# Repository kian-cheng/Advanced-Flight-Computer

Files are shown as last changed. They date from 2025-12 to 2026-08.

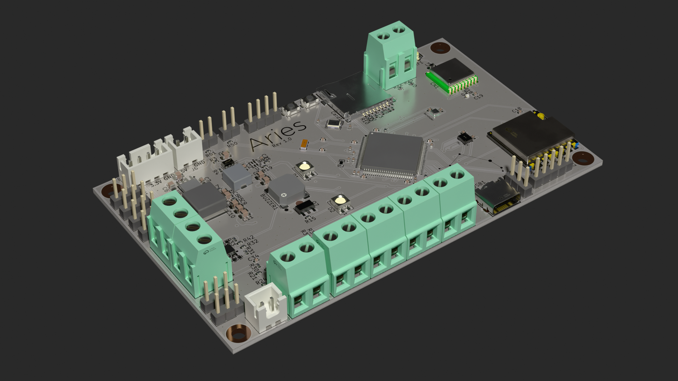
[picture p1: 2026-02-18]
CAD/Aries render.png

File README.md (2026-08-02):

# Advanced-Flight-Computer
A flight computer designed to be feature-rich and intuitive to use. Include features for dual deployment, ignition, active flight stabilisation and data logging. 

Before this, I've only made a simpler flight computer on a perfboard that does data logging and managing ignition and ejection. So this is my oppoturnity to make something more advanced on a PCB. 



## Features

- MCU: STM32H743VIT6
- Barometer: BMP 580
- IMU: ICM-45686
- GPS: ATGM336
- LORA: Ra-02
- USB-C
- Micro SD card reader
- 6 pyro channels
- 6 servo channels

## Schematic



## PCB layout





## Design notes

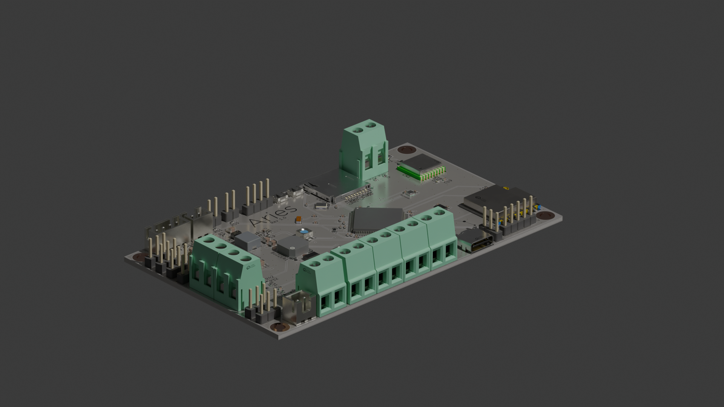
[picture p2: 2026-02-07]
CAD/Aries first render.png

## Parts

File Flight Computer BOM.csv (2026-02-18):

Item | Description | Cost (USD) | Quantity | Link
PCB + PCBA | 4 layer PCB from JLCPCB including shipping, although the ICM-45686 is out of stock so a 26 USD + shipping budget should be considered for getting it in the future. (2 is the minimum) | 289.85 | 1
PCB Shipping | Cheapest available SF express | 11.36 | 1
RF Antenna | For RA-02 433Mhz | 3.99 | 1 | https://www.waveshare.com/sma-433-antenna.htm
GPS Antenna | For GPS | 1.99 | 1 | https://www.waveshare.com/gnss-ceramic-antenna.htm
IPX to SMA | IPEX 1 specifically for RA-02 to Antenna | 0.69 | 1 | https://www.waveshare.com/sma-to-ipex-cable.htm?sku=21119
Waveshare shipping | Shipping for the three products above, cheapest available | 6 | 1
ICM-45686 | LCSC (only applicable when out of stock and backorder is needed) | 13.69 | 2 | https://www.lcsc.com/product-detail/C22459454.html
1x05 pins | LCSC (MPQ20) | 0.48 | 1 | https://www.lcsc.com/product-detail/C42431835.html?s_z=n_1x05
1x04 pins | LCSC (MPQ20) | 0.35 | 1 | https://www.lcsc.com/product-detail/C52016392.html
1x02 pins | LCSC (MPQ20) | 0.28 | 1 | https://www.lcsc.com/product-detail/C52016390.html
JST XH 4 pin | LCSC (MPQ10) | 0.53 | 1 | https://www.lcsc.com/product-detail/C144395.html?s_z=n_jst%2520xh%25204%2520pin
JST XH 2 pin | LCSC (MPQ20) | 0.71 | 1 | https://www.lcsc.com/product-detail/C158012.html
LCSC Shipping | Cheapest available | 5.51 | 1
Solder paste | Shipping can be free with vouchers (only required when ICM-45686 is out of stock) | 8.87 | 1 | https://shopee.com.my/product/279893497/15397824526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

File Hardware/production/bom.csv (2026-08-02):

Designator | Footprint | Quantity | Value | LCSC Part #
BUZZER1 | BUZ-SMD_4P-L7.5-W7.5-P7.59-TL | 1 | MLT-7525 | C95299
C1 | 0805 | 1 | 2.2 uf
C10, C11, C3, C4, C9 | 0805 | 5 | 22uF
C12 | 0603 | 1 | 2.7nF
C13 | 0603 | 1 | 33pF
C14, C15, C16, C17, C20, C21, C22, C23, C24, C25, C26, C31, C32 | 0402 | 13 | 100nF
C18 | 0402 | 1 | 0.1uF
C19 | 0402 | 1 | 10uF
C2, C7 | 0603 | 2 | 100nF
C27 | 0402 | 1 | 10pF
C28, C29 | 0402 | 2 | 2.2uF
C30, C33 | 0402 | 2 | 1uF
C34 | 0402 | 1 | 22nF
C36 | 0402 | 1 | 4.7uF
C37, C38, C39, C40 | 0402 | 4 | 20pF
C5 | 0805 | 1 | 10uF
C6 | 0805 | 1 | 10nF
C8 | 0805 | 1 | 47pF
CARD1 | TF-SMD_TF-01A | 1 | TF-01A | C91145
CN1 | COMM-SMD_18P-L10.1-W9.7-P1.1-TL_L76-LB | 1 | ATGM336H-6N-74 | C5804601
D1, D2 | LED_SK6812MINI_PLCC4_3.5x3.5mm_P1.75mm | 2 | SK6812MINI
D10, D3, D6, D7, D8, D9 | 0402 | 6 | LED | C25503345
D11 | 0402 | 1 | LED | C130723
D4 | 0402 | 1 | LED | C21260817
D5 | 0603 | 1 | LED | C22371297
J1 | PinHeader_1x03_P2.54mm_Vertical | 1 | Conn_01x03_Pin
J2 | PinHeader_1x04_P2.54mm_Vertical | 1 | Conn_01x04_Pin
J3, J4 | PinHeader_1x02_P2.54mm_Vertical | 2 | Conn_01x02_Pin
J5, J6 | JST_XH_B2B-XH-AM_1x02_P2.50mm_Vertical | 2 | Conn_01x02_Pin | C158012
J7 | PinHeader_1x05_P2.54mm_Vertical | 1 | Conn_01x05_Pin
J8 | JST_XH_B4B-XH-AM_1x04_P2.50mm_Vertical | 1 | Conn_01x04_Pin
L1 | L_Bourns_SRP5030T | 1 | 5.6uH | C46595886
L2 | L_Cenker_CKCS8040 | 1 | 3.6uH | C223037
L3 | 0603 | 1 | 47nH | C98076
L4 | L0603 | 1 | FCM1608KF-601T03 | C141723
M1, M2, M3, M4, M5, M6 | PinHeader_1x03_P2.54mm_Vertical | 6 | Motor_Servo
P1, P2, P3, P4, P5, P6, P7, P8 | CONN-TH_2P-P5.00_WJ500V-5.08-2P | 8 | WJ500V-5.08-2P-14-00A | C8465
Q1, Q2, Q3 | POWER-1212-8_L3.3-W3.3-P0.66-LS3.3-BL | 3 | SI7232DN-T1-GE3 | C144854
Q7 | SOT-89-3_L4.5-W2.4-P1.50-LS4.0-BR | 1 | 2N2222AU | C21714170
R1, R2 | 0402 | 2 | 5.1K
R10, R11, R12, R13, R14, R19, R30, R31, R33, R37, R38, R40, R41, R50, R51, R8, R9 | 0402 | 17 | 10K
R15, R16, R18, R25, R26, R27, R28, R32, R34, R35, R36, R39, R42, R43 | 0402 | 14 | 1k
R17 | 0402 | 1 | 470
R20, R4, R6 | 0402 | 3 | 22.1k
R21 | 0402 | 1 | 120k
R22 | 0402 | 1 | 200K
R23 | 0402 | 1 | 40K
R24 | 0402 | 1 | 550
R29 | 0402 | 1 | 75k
R3 | 0402 | 1 | 100k
R44 | 0402 | 1 | 430
R5 | 0402 | 1 | 115k
R7 | 0402 | 1 | 15.8k
RF1 | IPEX-SMD_BWIPX-1-001E | 1 | BWIPX-1-001E | C496552
SW1, SW2 | SW-SMD_L3.9-W3.0-P4.45 | 2 | TS-1088-AR02016 | C720477
U1 | LGA-10_L2.0-W2.0-P0.50-TL_BMP580 | 1 | BMP580 | C22391138
U10, U11, U12, U13, U8, U9 | F0603 | 6 | 0438006.WRGT | C206962
U2 | LQFP-100_14x14mm_P0.5mm | 1 | STM32H743VITx | C114409
U3 | LGA-14_L3.0-W2.5-P0.50-TL | 1 | ICM-45686 | C22459454
U4 | SOT-23-6_L2.9-W1.6-P0.95-LS2.8-BL | 1 | LMR51430XDDCR | C5185863
U5 | SOIC-8_L4.9-W3.9-P1.27-LS6.0-BL-EP-1 | 1 | AP64501SP-13 | C2071517
U6 | WIRELM-SMD_RA-02-BL | 1 | RA-02 | C90039
U7 | VQFN-HR-12_L2.5-W2.0-P0.50-BL | 1 | TPS2121RUXR | C485916
USB1 | USB-C-SMD_TYPE-C16PIN | 1 | TYPE-C16PIN | C393939
X1 | CRYSTAL-SMD_4P-L3.2-W2.5-BL | 1 | X322525MOB4SI | C9006
X2 | FC-135R_L3.2-W1.5 | 1 | Q13FC1350000400 | C32346

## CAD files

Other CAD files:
CAD/Aries.blend

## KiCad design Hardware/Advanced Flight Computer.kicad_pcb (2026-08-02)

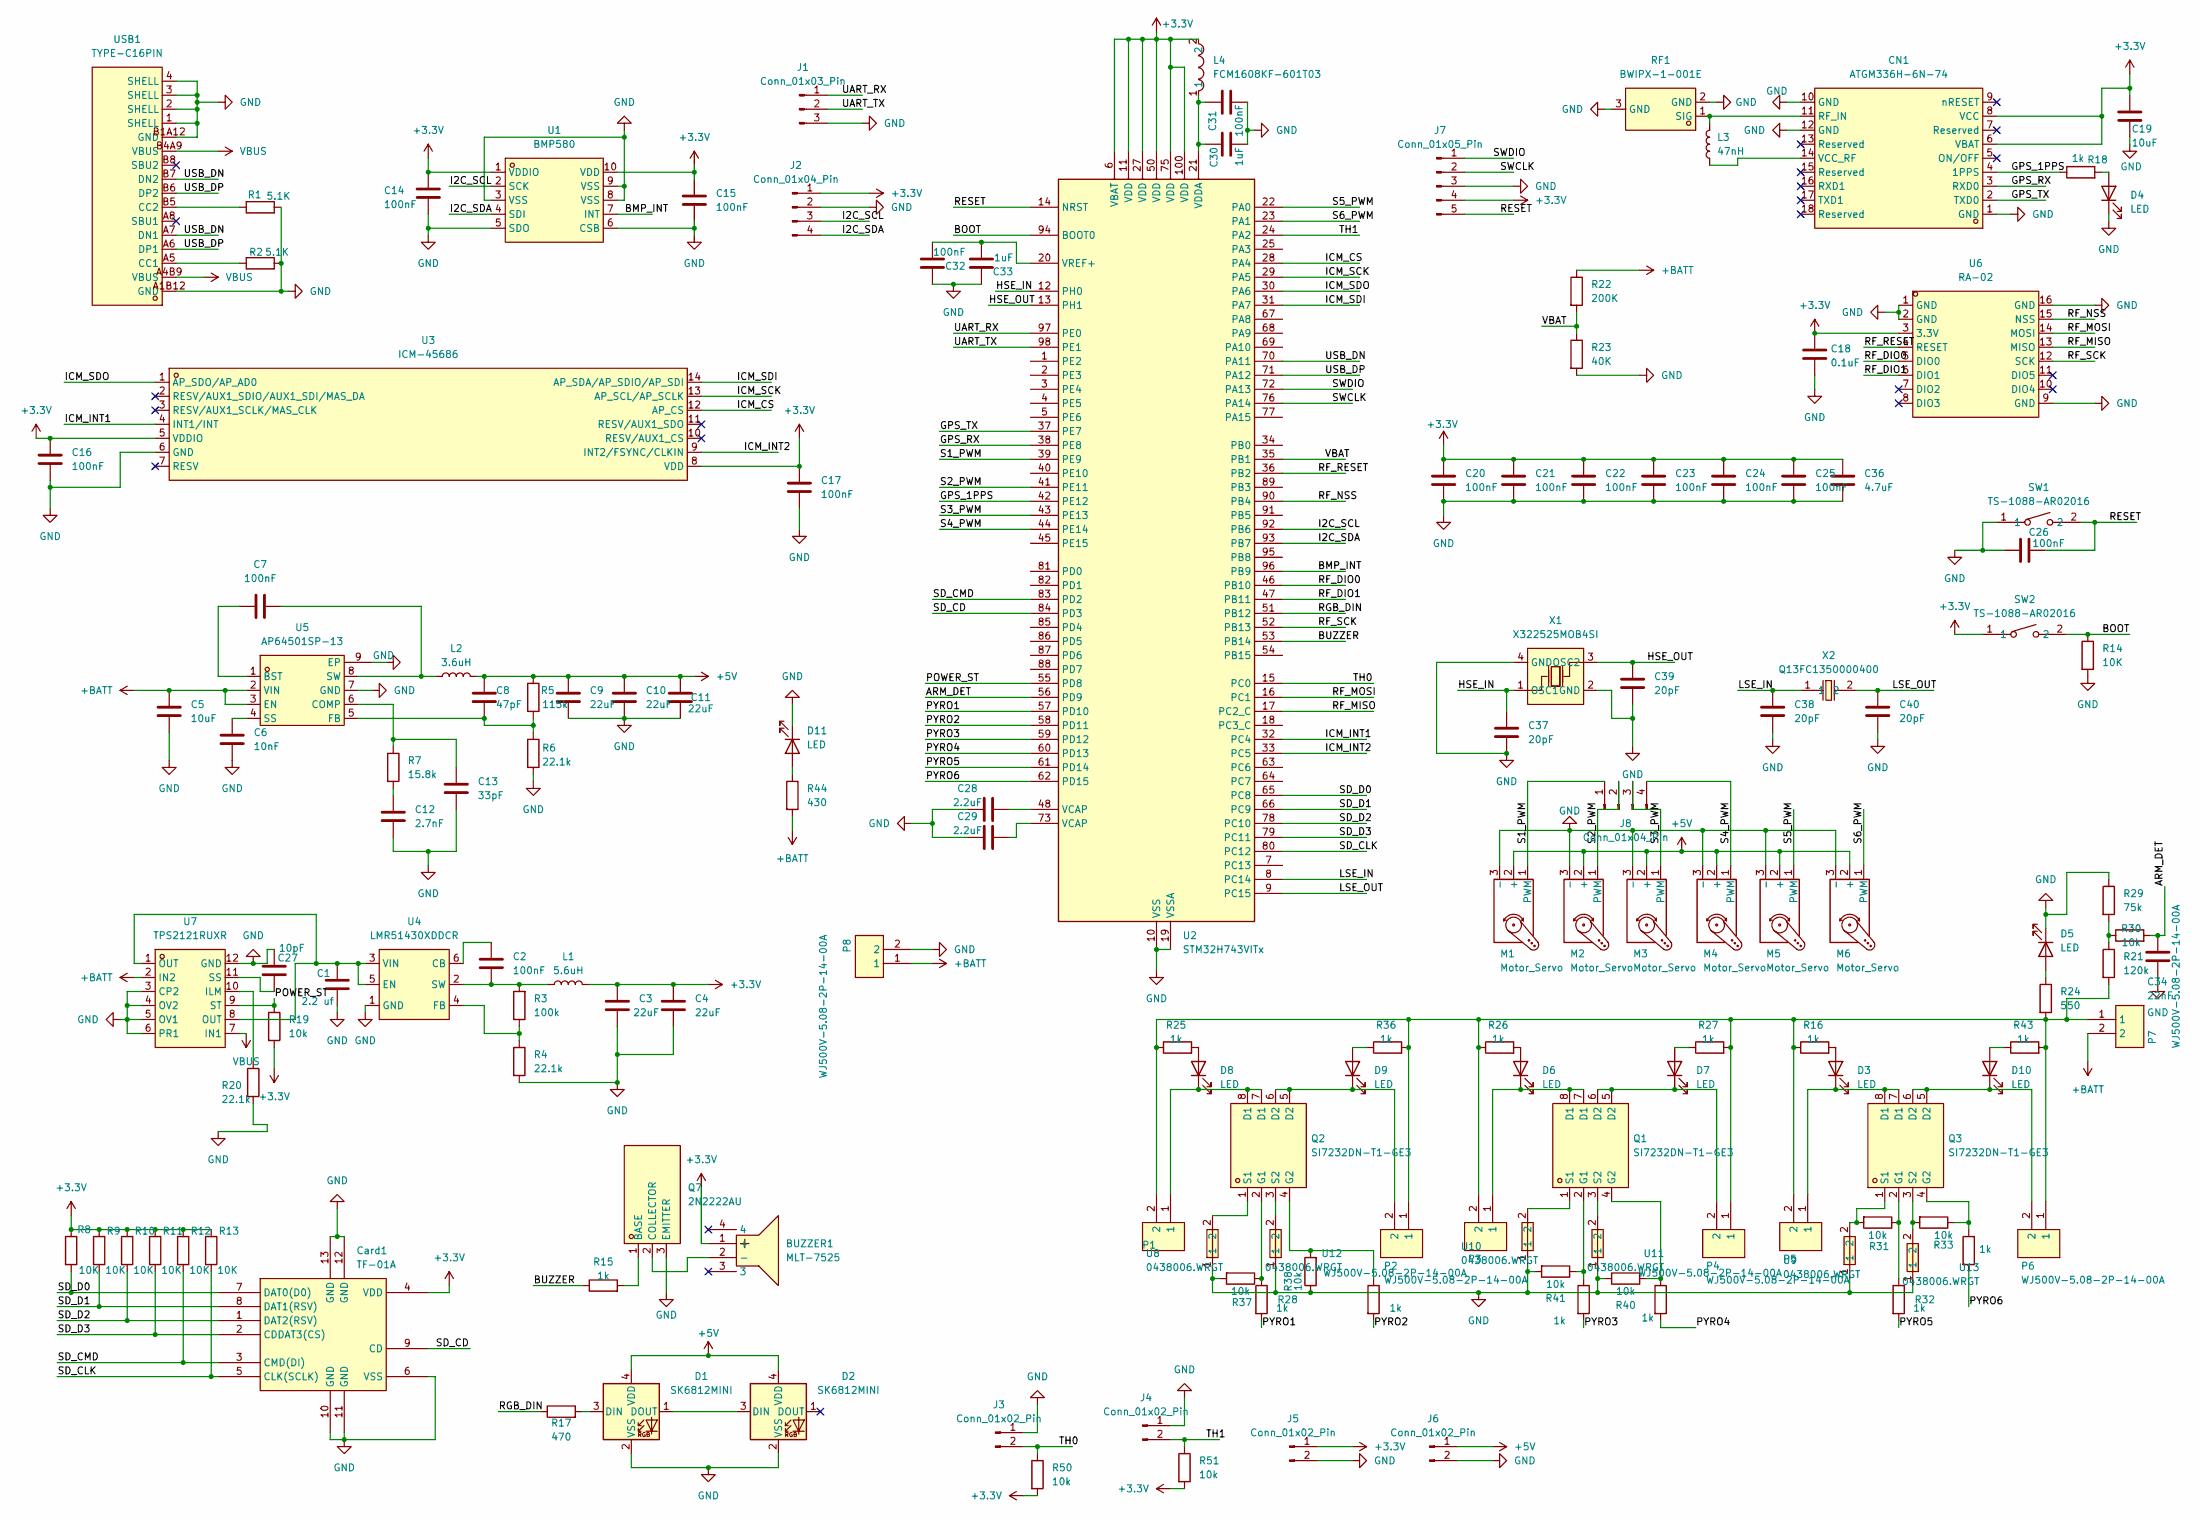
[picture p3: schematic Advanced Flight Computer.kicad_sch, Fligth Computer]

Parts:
BUZZER1: MLT-7525; BUZ-SMD_4P-L7.5-W7.5-P7.59-TL; LCSC Part C95299
C1: 2.2 uf; C_0805_2012Metric
C2, C7: 100nF; C_0603_1608Metric
C3, C4, C9, C10, C11: 22uF; C_0805_2012Metric
C5: 10uF; C_0805_2012Metric
C6: 10nF; C_0805_2012Metric
C8: 47pF; C_0805_2012Metric
C12: 2.7nF; C_0603_1608Metric
C13: 33pF; C_0603_1608Metric
C14, C15, C16, C17, C20, C21, C22, C23, C24, C25, C26, C31, C32: 100nF; C_0402_1005Metric
C18: 0.1uF; C_0402_1005Metric
C19: 10uF; C_0402_1005Metric
C27: 10pF; C_0402_1005Metric
C28, C29: 2.2uF; C_0402_1005Metric
C30, C33: 1uF; C_0402_1005Metric
C34: 22nF; C_0402_1005Metric
C36: 4.7uF; C_0402_1005Metric
C37, C38, C39, C40: 20pF; C_0402_1005Metric
CN1: ATGM336H-6N-74; COMM-SMD_18P-L10.1-W9.7-P1.1-TL_L76-LB; LCSC Part C5804601
Card1: TF-01A; TF-SMD_TF-01A; LCSC Part C91145
D1, D2: SK6812MINI; LED_SK6812MINI_PLCC4_3.5x3.5mm_P1.75mm
D3, D4, D6, D7, D8, D9, D10: LED; LED_0402_1005Metric
D5: LED; LED_0603_1608Metric
D11: LED; LED_0402_1005Metric; LCSC C130723
J1: Conn_01x03_Pin; PinHeader_1x03_P2.54mm_Vertical
J2: Conn_01x04_Pin; PinHeader_1x04_P2.54mm_Vertical
J3, J4: Conn_01x02_Pin; PinHeader_1x02_P2.54mm_Vertical
J5, J6: Conn_01x02_Pin; JST_XH_B2B-XH-AM_1x02_P2.50mm_Vertical; LCSC C158012
J7: Conn_01x05_Pin; PinHeader_1x05_P2.54mm_Vertical
J8: Conn_01x04_Pin; JST_XH_B4B-XH-AM_1x04_P2.50mm_Vertical
L1: 5.6uH; L_Bourns_SRP5030T; LCSC C46595886
L2: 3.6uH; L_Cenker_CKCS8040; LCSC C223037
L3: 47nH; L_0603_1608Metric_Pad1.05x0.95mm_HandSolder; LCSC C98076
L4: FCM1608KF-601T03; L0603; LCSC Part C141723
M1, M2, M3, M4, M5, M6: Motor_Servo; PinHeader_1x03_P2.54mm_Vertical
P1, P2, P3, P4, P5, P6, P7, P8: WJ500V-5.08-2P-14-00A; CONN-TH_2P-P5.00_WJ500V-5.08-2P; LCSC Part C8465
Q1, Q2, Q3: SI7232DN-T1-GE3; POWER-1212-8_L3.3-W3.3-P0.66-LS3.3-BL; LCSC Part C144854
Q7: 2N2222AU; SOT-89-3_L4.5-W2.4-P1.50-LS4.0-BR; LCSC Part C21714170
R1, R2: 5.1K; R_0402_1005Metric
R3: 100k; R_0402_1005Metric
R4, R6, R20: 22.1k; R_0402_1005Metric
R5: 115k; R_0402_1005Metric
R7: 15.8k; R_0402_1005Metric
R8, R9, R10, R11, R12, R13, R14: 10K; R_0402_1005Metric
R15, R16, R18, R25, R26, R27, R28, R32, R34, R35, R36, R39, R42, R43: 1k; R_0402_1005Metric
R17: 470; R_0402_1005Metric
R19, R30, R31, R33, R37, R38, R40, R41, R50, R51: 10k; R_0402_1005Metric
R21: 120k; R_0402_1005Metric
R22: 200K; R_0402_1005Metric
R23: 40K; R_0402_1005Metric
R24: 550; R_0402_1005Metric
R29: 75k; R_0402_1005Metric
R44: 430; R_0402_1005Metric
RF1: BWIPX-1-001E; IPEX-SMD_BWIPX-1-001E; LCSC Part C496552
SW1, SW2: TS-1088-AR02016; SW-SMD_L3.9-W3.0-P4.45; LCSC Part C720477
U1: BMP580; LGA-10_L2.0-W2.0-P0.50-TL_BMP580; LCSC Part C22391138
U2: STM32H743VITx; LQFP-100_14x14mm_P0.5mm
U3: ICM-45686; LGA-14_L3.0-W2.5-P0.50-TL; LCSC Part C22459454
U4: LMR51430XDDCR; SOT-23-6_L2.9-W1.6-P0.95-LS2.8-BL; LCSC Part C5185863
U5: AP64501SP-13; SOIC-8_L4.9-W3.9-P1.27-LS6.0-BL-EP-1; LCSC Part C2071517
U6: RA-02; WIRELM-SMD_RA-02-BL; LCSC Part C90039
U7: TPS2121RUXR; VQFN-HR-12_L2.5-W2.0-P0.50-BL; LCSC Part C485916
U8, U9, U10, U11, U12, U13: 0438006.WRGT; F0603; LCSC Part C206962
USB1: TYPE-C16PIN; USB-C-SMD_TYPE-C16PIN; LCSC Part C393939
X1: X322525MOB4SI; CRYSTAL-SMD_4P-L3.2-W2.5-BL; LCSC Part C9006
X2: Q13FC1350000400; FC-135R_L3.2-W1.5; LCSC Part C32346

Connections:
+3.3V: BUZZER1.1 (+), C3.1, C4.1, C14.1, C15.1, C16.1, C17.1, C18.1, C19.1, C20.1, C21.1, C22.1, C23.1, C24.1, C25.1, C36.1, CN1.6 (VBAT), CN1.8 (VCC), Card1.4 (VDD), J2.1, J5.1, J7.4, L1.2, L4.2, R8.1, R9.1, R10.1, R11.1, R12.1, R13.1, R19.2, R50.2, R51.2, SW2.1, U1.1 (VDDIO), U1.10 (VDD), U2.6 (VBAT), U2.11 (VDD), U2.27 (VDD), U2.50 (VDD), U2.75 (VDD), U2.100 (VDD), U3.5 (VDDIO), U3.8 (VDD), U6.3 (3.3V)
+5V: C8.1, C9.1, C10.1, C11.1, D1.4 (VDD), D2.4 (VDD), J6.1, L2.2, M1.2 (+), M2.2 (+), M3.2 (+), M4.2 (+), M5.2 (+), M6.2 (+), R5.1
+BATT: C5.1, P7.2, P8.1, R22.1, R44.2, U5.2 (VIN), U5.3 (EN), U7.2 (IN2)
/ARM_DET: C34.1, R30.2, U2.56 (PD9)
/BMP_INT: U1.7 (INT), U2.96 (PB9)
/BOOT: R14.1, SW2.2, U2.94 (BOOT0)
/BUZZER: R15.1, U2.53 (PB14)
/GPS_1PPS: CN1.4 (1PPS), R18.1, U2.42 (PE12)
/GPS_RX: CN1.3 (RXD0), U2.38 (PE8)
/GPS_TX: CN1.2 (TXD0), U2.37 (PE7)
/HSE_IN: C37.1, U2.12 (PH0), X1.1 (OSC1)
/HSE_OUT: C39.1, U2.13 (PH1), X1.3 (OSC2)
/I2C_SCL: J2.3, U1.2 (SCK), U2.92 (PB6)
/I2C_SDA: J2.4, U1.4 (SDI), U2.93 (PB7)
/ICM_CS: U2.28 (PA4), U3.12 (AP_CS)
/ICM_INT1: U2.32 (PC4), U3.4 (INT1/INT)
/ICM_INT2: U2.33 (PC5), U3.9 (INT2/FSYNC/CLKIN)
/ICM_SCK: U2.29 (PA5), U3.13 (AP_SCL/AP_SCLK)
/ICM_SDI: U2.31 (PA7), U3.14 (AP_SDA/AP_SDIO/AP_SDI)
/ICM_SDO: U2.30 (PA6), U3.1 (AP_SDO/AP_AD0)
/LSE_IN: C38.1, U2.8 (PC14), X2.1
/LSE_OUT: C40.1, U2.9 (PC15), X2.2
/POWER_ST: R19.1, U2.55 (PD8), U7.9 (ST)
/PYRO1: R28.2, U2.57 (PD10)
/PYRO2: R34.2, U2.58 (PD11)
/PYRO3: R35.2, U2.59 (PD12)
/PYRO4: R39.2, U2.60 (PD13)
/PYRO5: R32.2, U2.61 (PD14)
/PYRO6: R42.2, U2.62 (PD15)
/RESET: C26.2, J7.5, SW1.2, U2.14 (NRST)
/RF_DIO0: U2.46 (PB10), U6.5 (DIO0)
/RF_DIO1: U2.47 (PB11), U6.6 (DIO1)
/RF_MISO: U2.17 (PC2_C), U6.13 (MISO)
/RF_MOSI: U2.16 (PC1), U6.14 (MOSI)
/RF_NSS: U2.90 (PB4), U6.15 (NSS)
/RF_RESET: U2.36 (PB2), U6.4 (RESET)
/RF_SCK: U2.52 (PB13), U6.12 (SCK)
/RGB_DIN: R17.1, U2.51 (PB12)
/S1_PWM: J8.1, M1.1 (PWM), U2.39 (PE9)
/S2_PWM: J8.2, M2.1 (PWM), U2.41 (PE11)
/S3_PWM: J8.3, M3.1 (PWM), U2.43 (PE13)
/S4_PWM: J8.4, M4.1 (PWM), U2.44 (PE14)
/S5_PWM: M5.1 (PWM), U2.22 (PA0)
/S6_PWM: M6.1 (PWM), U2.23 (PA1)
/SD_CD: Card1.9 (CD), U2.84 (PD3)
/SD_CLK: Card1.5 (CLK(SCLK)), R13.2, U2.80 (PC12)
/SD_CMD: Card1.3 (CMD(DI)), R12.2, U2.83 (PD2)
/SD_D0: Card1.7 (DAT0(D0)), R8.2, U2.65 (PC8)
/SD_D1: Card1.8 (DAT1(RSV)), R9.2, U2.66 (PC9)
/SD_D2: Card1.1 (DAT2(RSV)), R10.2, U2.78 (PC10)
/SD_D3: Card1.2 (CDDAT3(CS)), R11.2, U2.79 (PC11)
/SWCLK: J7.2, U2.76 (PA14)
/SWDIO: J7.1, U2.72 (PA13)
/TH0: J3.2, R50.1, U2.15 (PC0)
/TH1: J4.2, R51.1, U2.24 (PA2)
/UART_RX: J1.1, U2.97 (PE0)
/UART_TX: J1.2, U2.98 (PE1)
/USB_DN: U2.70 (PA11), USB1.A7 (DN1), USB1.B7 (DN2)
/USB_DP: U2.71 (PA12), USB1.A6 (DP1), USB1.B6 (DP2)
/VBAT: R22.2, R23.1, U2.35 (PB1)
GND: C1.2, C3.2, C4.2, C5.2, C6.2, C9.2, C10.2, C11.2, C12.2, C13.2, C14.2, C15.2, C16.2, C17.2, C18.2, C19.2, C20.2, C21.2, C22.2, C23.2, C24.2, C25.2, C26.1, C27.1, C28.1, C29.1, C30.2, C31.2, C32.1, C33.1, C34.2, C36.2, C37.2, C38.2, C39.2, C40.2, CN1.1 (GND), CN1.10 (GND), CN1.12 (GND), Card1.6 (VSS), Card1.10 (GND), Card1.11 (GND), Card1.12 (GND), Card1.13 (GND), D1.2 (VSS), D2.2 (VSS), D4.1 (K), D5.1 (K), D11.1 (K), J1.3, J2.2, J3.1, J4.1, J5.2, J6.2, J7.3, M1.3 (-), M2.3 (-), M3.3 (-), M4.3 (-), M5.3 (-), M6.3 (-), P8.2, Q7.3 (EMITTER), R1.2, R2.2, R4.2, R6.2, R14.2, R20.2, R23.2, R29.1, R37.2, R38.1, R40.1, R41.2, RF1.2 (GND), RF1.3 (GND), SW1.1, U1.3 (VSS), U1.5 (SDO), U1.6 (CSB), U1.8 (VSS), U1.9 (VSS), U2.10 (VSS), U2.19 (VSSA), U2.26 (VSS), U2.49 (VSS), U2.74 (VSS), U2.99 (VSS), U3.6 (GND), U4.1 (GND), U5.7 (GND), U5.9 (EP), U6.1 (GND), U6.2 (GND), U6.9 (GND), U6.16 (GND), U7.3 (CP2), U7.4 (OV2), U7.5 (OV1), U7.6 (PR1), U7.12 (GND), U8.1, U9.1, U10.1, U11.1, U12.1, U13.1, USB1.1 (SHELL), USB1.2 (SHELL), USB1.3 (SHELL), USB1.4 (SHELL), USB1.A1B12 (GND), USB1.B1A12 (GND), X1.2 (GND), X1.4 (GND)
unnamed: BUZZER1.2 (-), Q7.2 (COLLECTOR)
unnamed: C12.1, R7.2
unnamed: C28.2, U2.48 (VCAP)
unnamed: C29.2, U2.73 (VCAP)
unnamed: CN1.11 (RF_IN), L3.2, RF1.1 (SIG)
unnamed: CN1.14 (VCC_RF), L3.1
unnamed: D1.3 (DIN), R17.2
unnamed: D1.1 (DOUT), D2.3 (DIN)
unnamed: D3.2 (A), R16.2
unnamed: D3.1 (K), P5.1, Q3.7 (D1), Q3.8 (D1)
unnamed: D4.2 (A), R18.2
unnamed: D5.2 (A), R24.1
unnamed: D6.2 (A), R26.2
unnamed: D6.1 (K), P3.1, Q1.7 (D1), Q1.8 (D1)
unnamed: D7.2 (A), R27.1
unnamed: D7.1 (K), P4.2, Q1.5 (D2), Q1.6 (D2)
unnamed: D8.2 (A), R25.2
unnamed: D8.1 (K), P1.1, Q2.7 (D1), Q2.8 (D1)
unnamed: D9.2 (A), R36.1
unnamed: D9.1 (K), P2.2, Q2.5 (D2), Q2.6 (D2)
unnamed: D10.2 (A), R43.1
unnamed: D10.1 (K), P6.2, Q3.5 (D2), Q3.6 (D2)
unnamed: D11.2 (A), R44.1
unnamed: P1.2, P2.1, P3.2, P4.1, P5.2, P6.1, P7.1, R16.1, R21.2, R24.2, R25.1, R26.1, R27.2, R36.2, R43.2
unnamed: Q1.2 (G1), R35.1, R41.1
unnamed: Q1.4 (G2), R39.1, R40.2
unnamed: Q1.1 (S1), U10.2
unnamed: Q1.3 (S2), U11.2
unnamed: Q2.2 (G1), R28.1, R37.1
unnamed: Q2.4 (G2), R34.1, R38.2
unnamed: Q2.1 (S1), U8.2
unnamed: Q2.3 (S2), U12.2
unnamed: Q3.2 (G1), R31.1, R32.1
unnamed: Q3.4 (G2), R33.1, R42.1
unnamed: Q3.1 (S1), R31.2, U9.2
unnamed: Q3.3 (S2), R33.2, U13.2
unnamed: Q7.1 (BASE), R15.2
unnamed: R21.1, R29.2, R30.1
unnamed: C30.1, C31.1, L4.1, U2.21 (VDDA)
unnamed: C32.2, C33.2, U2.20 (VREF+)
unnamed: C2.1, U4.6 (CB)
unnamed: C1.1, U4.3 (VIN), U4.5 (EN), U7.1 (OUT), U7.8 (OUT)
unnamed: R3.1, R4.1, U4.4 (FB)
unnamed: C2.2, L1.1, R3.2, U4.2 (SW)
unnamed: C7.1, U5.1 (BST)
unnamed: C13.1, R7.1, U5.6 (COMP)
unnamed: C8.2, R5.2, R6.1, U5.5 (FB)
unnamed: C6.1, U5.4 (SS)
unnamed: C7.2, L2.1, U5.8 (SW)
unnamed: R20.1, U7.10 (ILM)
unnamed: C27.2, U7.11 (SS)
unnamed: R2.1, USB1.A5 (CC1)
unnamed: R1.1, USB1.B5 (CC2)
VBUS: U7.7 (IN1), USB1.A4B9 (VBUS), USB1.B4A9 (VBUS)

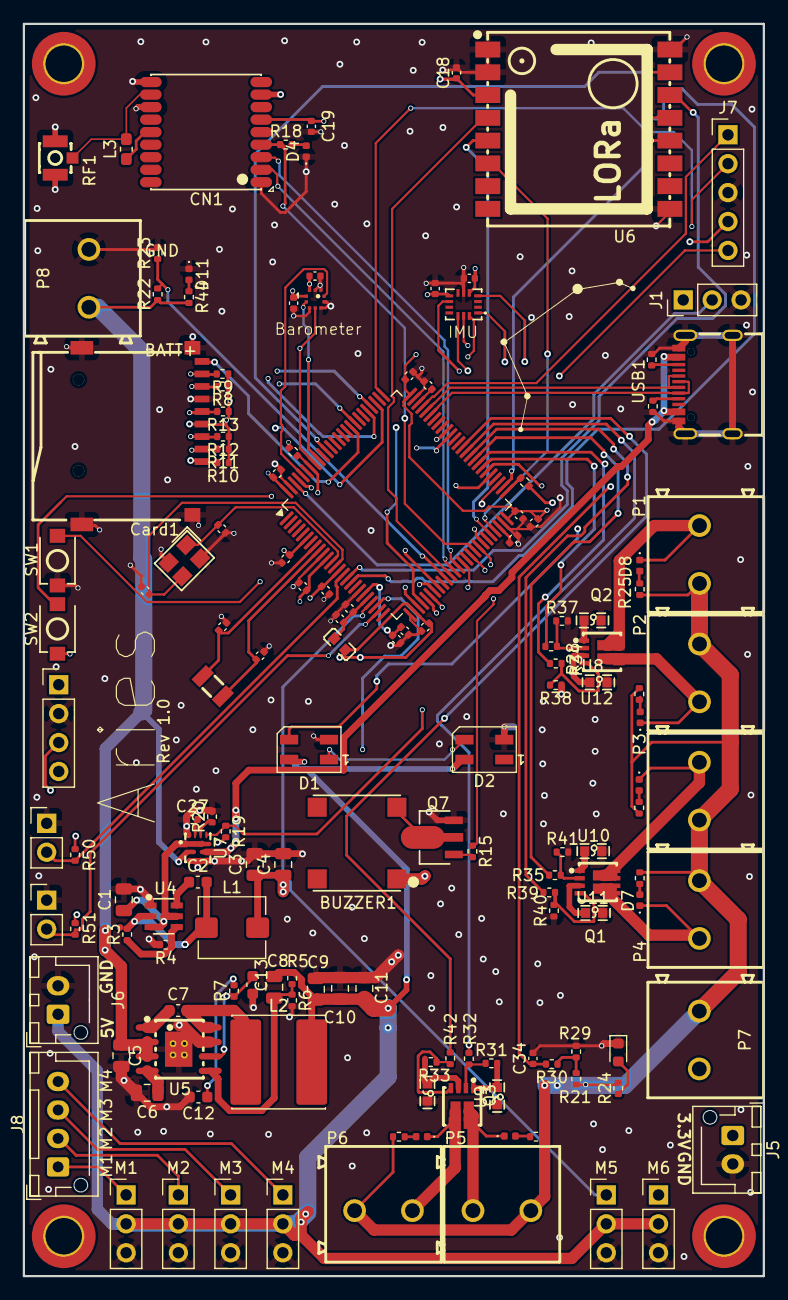
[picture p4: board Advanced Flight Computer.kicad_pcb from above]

Board: 4 copper layers, 65.0 x 110.0 mm, 148 parts (0 on the bottom side), 115 nets.

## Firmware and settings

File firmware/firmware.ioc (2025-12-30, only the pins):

Mcu.UserName=STM32H743VITx
PA0.Signal=S_TIM2_CH1_ETR
PA1.Signal=S_TIM2_CH2
PA11.Signal=USB_OTG_FS_DM
PA12.Signal=USB_OTG_FS_DP
PA2.GPIO_Label=TH1
PA2.Signal=ADCx_INP14
PA4.Signal=SPI1_NSS
PA5.Signal=SPI1_SCK
PA6.Signal=SPI1_MISO
PB1.GPIO_Label=VBAT
PB1.Signal=ADCx_INP5
PB10.GPIO_Label=RF_DIO0
PB10.Signal=GPXTI10
PB11.GPIO_Label=RF_DIO1
PB11.Signal=GPXTI11
PB12.GPIO_Label=RGB_DIN
PB12.Signal=GPIO_Output
PB13.Signal=SPI2_SCK
PB14.GPIO_Label=BUZZER
PB14.Signal=S_TIM12_CH1
PB2.GPIO_Label=RF_RESET
PB2.Signal=GPIO_Input
PB6.Signal=I2C1_SCL
PB7.Signal=I2C1_SDA
PB9.GPIO_Label=BMP_INT
PB9.Signal=GPXTI9
PC0.GPIO_Label=TH0
PC0.Signal=ADCx_INP10
PC1.Signal=SPI2_MOSI
PC10.Signal=SDMMC1_D2
PC11.Signal=SDMMC1_D3
PC12.Signal=SDMMC1_CK
PC2_C.Signal=SPI2_MISO
PC4.GPIO_Label=ICM_INT1
PC4.Signal=GPXTI4
PC5.GPIO_Label=ICM_INT2
PC5.Signal=GPXTI5
PC8.Signal=SDMMC1_D0
PC9.Signal=SDMMC1_D1
PD10.Signal=GPIO_Output
PD11.Signal=GPIO_Output
PD12.Signal=GPIO_Output
PD13.Signal=GPIO_Output
PD14.Signal=GPIO_Output
PD15.Signal=GPIO_Output
PD2.Signal=SDMMC1_CMD
PD3.GPIO_Label=SD_CD
PD3.Signal=GPIO_Input
PD7.Signal=SPI1_MOSI
PD8.Signal=GPIO_Input
PD9.GPIO_Label=ARM_DET
PD9.Signal=GPIO_Input
PE0.Signal=UART8_RX
PE1.Signal=UART8_TX
PE11.Signal=S_TIM1_CH2
PE12.GPIO_Label=GPS_1PPS
PE12.Signal=GPXTI12
PE13.Signal=S_TIM1_CH3
PE14.Signal=S_TIM1_CH4
PE7.Signal=UART7_RX
PE8.Signal=UART7_TX
PE9.Signal=S_TIM1_CH1

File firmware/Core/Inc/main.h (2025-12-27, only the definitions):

#define TH0_Pin GPIO_PIN_0
#define TH0_GPIO_Port GPIOC
#define TH1_Pin GPIO_PIN_2
#define TH1_GPIO_Port GPIOA
#define ICM_INT1_Pin GPIO_PIN_4
#define ICM_INT1_GPIO_Port GPIOC
#define ICM_INT2_Pin GPIO_PIN_5
#define ICM_INT2_GPIO_Port GPIOC
#define VBAT_Pin GPIO_PIN_1
#define VBAT_GPIO_Port GPIOB
#define RF_RESET_Pin GPIO_PIN_2
#define RF_RESET_GPIO_Port GPIOB
#define GPS_1PPS_Pin GPIO_PIN_12
#define GPS_1PPS_GPIO_Port GPIOE
#define RF_DIO0_Pin GPIO_PIN_10
#define RF_DIO0_GPIO_Port GPIOB
#define RF_DIO1_Pin GPIO_PIN_11
#define RF_DIO1_GPIO_Port GPIOB
#define RGB_DIN_Pin GPIO_PIN_12
#define RGB_DIN_GPIO_Port GPIOB
#define BUZZER_Pin GPIO_PIN_14
#define BUZZER_GPIO_Port GPIOB
#define ARM_DET_Pin GPIO_PIN_9
#define ARM_DET_GPIO_Port GPIOD
#define SD_CD_Pin GPIO_PIN_3
#define SD_CD_GPIO_Port GPIOD
#define BMP_INT_Pin GPIO_PIN_9
#define BMP_INT_GPIO_Port GPIOB

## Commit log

2025-12-01 Create folder and files for PCB
    [Advanced Flight Computer.kicad_pcb, Advanced Flight Computer.kicad_sch]
2025-12-01 started schematics and added libraries
    [Advanced Flight Computer.kicad_pcb, Advanced Flight Computer.kicad_sch]
2025-12-07 Added symbols, wired up some components in schematic.
    [Advanced Flight Computer.kicad_sch]
2025-12-22 Update with latest changes
    [Advanced Flight Computer.kicad_sch]
2025-12-28 Update README with schematic and PCB layout images
    Added images for schematic and PCB layout.
2025-12-29 Update schematic image in README
2026-01-05 Update PCB layout image in README.md
2026-01-06 Update Flight Computer BOM with new links and items
    [Flight Computer BOM.csv]
2026-01-06 Update Flight Computer BOM with LCSC Shipping
    Added LCSC Shipping item to the BOM.
    [Flight Computer BOM.csv]
2026-01-06 Update Flight Computer BOM.csv
    [Flight Computer BOM.csv]
2026-02-07 Update to Render, PCB and Schematic
    [Advanced Flight Computer.kicad_sch, Aries.blend, bom.csv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]
2026-02-07 Update to PCB
    [Advanced Flight Computer.kicad_pcb]
2026-02-07 Update images in README for schematic and PCB layout
2026-02-07 Update BOM
    [Flight Computer BOM.csv]
2026-02-08 Revise Flight Computer BOM with new components
    Updated item descriptions and added a new JST XH 4 pin entry.
    [Flight Computer BOM.csv]
2026-02-08 Update Flight Computer BOM with new items
    Added new item '1x05 pins' to the BOM with details.
    [Flight Computer BOM.csv]
2026-02-08 Revise Flight Computer BOM entries and links
    Updated the Flight Computer BOM with corrected item entries and links.
    [Flight Computer BOM.csv]
2026-02-18 PCB fixes
    [Advanced Flight Computer.kicad_pcb]

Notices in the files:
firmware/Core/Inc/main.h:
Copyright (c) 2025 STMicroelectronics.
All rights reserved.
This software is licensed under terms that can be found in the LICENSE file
